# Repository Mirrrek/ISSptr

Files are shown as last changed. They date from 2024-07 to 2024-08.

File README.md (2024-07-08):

# ISSptr

A lil thing that points towards the ISS.

## Required hardware

- [The PCB](https://github.com/Mirrrek/ISSptr/tree/main/schematic), obviously, including:
  - [ESP32-WROOM-32-N4](https://jlcpcb.com/partdetail/EspressifSystems-ESP32_WROOM_32N4/C82899) Microcontroller
  - [QMC5883L](https://jlcpcb.com/partdetail/Qst-QMC5883L/C976032) Magnetometer
  - [ULN2003AD](https://jlcpcb.com/partdetail/TexasInstruments-ULN2003AD/C908113) Transistor Array
  - [AMS1117-3.3](https://jlcpcb.com/partdetail/Advanced_MonolithicSystems-AMS1117_33/C6186) Voltage Regulator
  - [BC817](https://jlcpcb.com/partdetail/Shikues-BC817/C475629) NPN Transistors
  - [TYPE-C-31-M-12](https://jlcpcb.com/partdetail/Korean_HropartsElec-TYPE_C_31_M12/C165948) USB-C Connector
  - [B5B-XH-A(LF)(SN)](https://jlcpcb.com/partdetail/Jst-B5B_XH_A_LF_SN/C157991) Connector
  - Some 0603 resistors and capacitors
- A servo motor (e.g. _SG90_)
- An unipolar stepper motor (e.g. _28BYJ-48_)
- 6-Channel slip ring

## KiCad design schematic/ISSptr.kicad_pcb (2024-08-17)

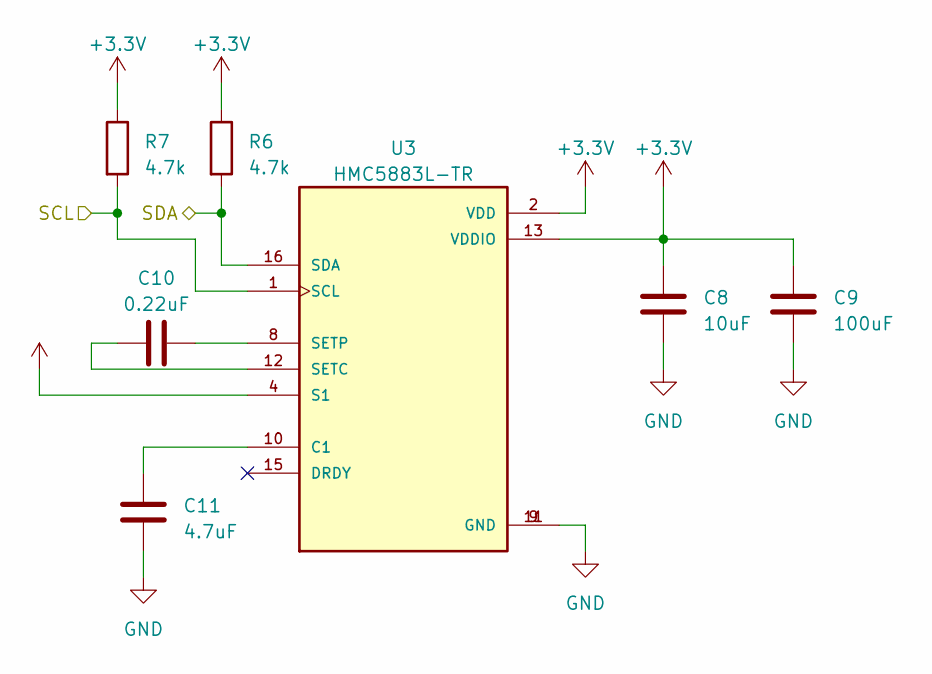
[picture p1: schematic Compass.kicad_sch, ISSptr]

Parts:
C8: 10uF; C_0603_1608Metric; LCSC C19702
C9: 100uF; C_0603_1608Metric; LCSC C730416
C10: 0.22uF; C_0603_1608Metric; LCSC C472764
C11: 4.7uF; C_0603_1608Metric; LCSC C307469
R6, R7: 4.7k; R_0603_1608Metric; LCSC C23162
U3: HMC5883L-TR; XDCR_HMC5883L-TR; PARTREV E; LCSC C976032

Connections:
+3.3V: C8.1, C9.1, R6.1, R7.1, U3.2 (VDD), U3.4 (S1), U3.13 (VDDIO); also elsewhere on the board
/Compass/SCL: R7.2, U3.1 (SCL); also elsewhere on the board
/Compass/SDA: R6.2, U3.16 (SDA); also elsewhere on the board
GND: C8.2, C9.2, C11.1, U3.9 (GND), U3.11 (GND); also elsewhere on the board
unnamed: C11.2, U3.10 (C1)
unnamed: C10.1, U3.12 (SETC)
unnamed: C10.2, U3.8 (SETP)

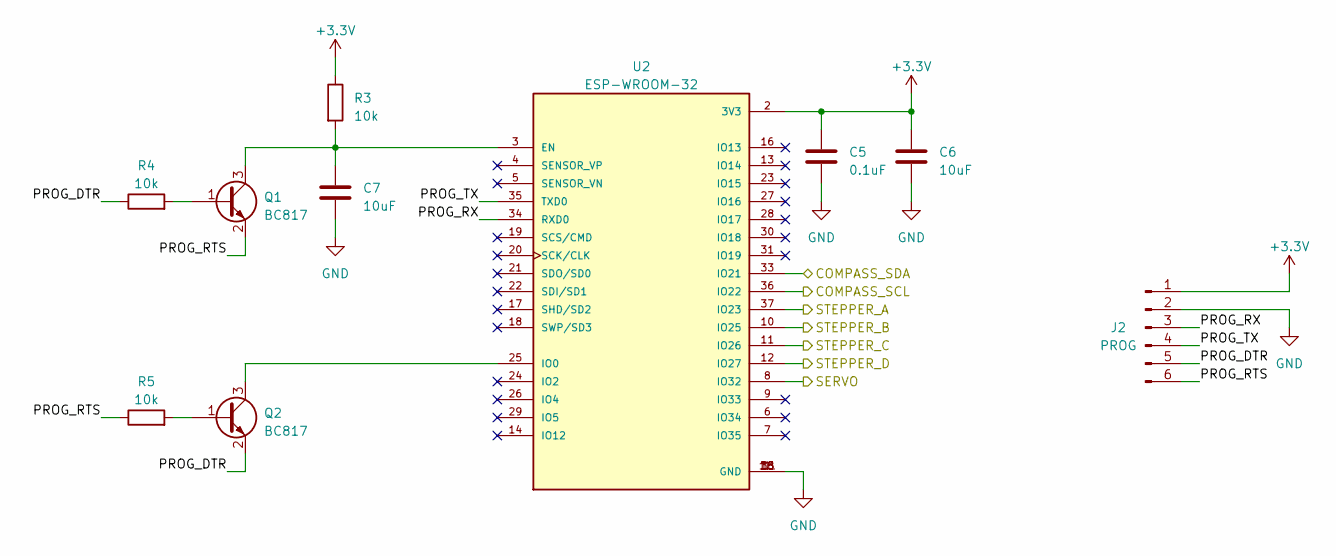
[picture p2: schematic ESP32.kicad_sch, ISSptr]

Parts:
C5: 0.1uF; C_0603_1608Metric; LCSC C1591
C6, C7: 10uF; C_0603_1608Metric; LCSC C19702
J2: PROG; PinHeader_1x06_P2.54mm_Vertical
Q1, Q2: BC817; SOT-23; LCSC C475629
R3, R4, R5: 10k; R_0603_1608Metric; LCSC C25804
U2: ESP-WROOM-32; MODULE_ESP-WROOM-32; LCSC C82899

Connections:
+3.3V: C5.1, C6.1, J2.1, R3.1, U2.2 (3V3); also elsewhere on the board
/Compass/SCL: U2.36 (IO22); also elsewhere on the board
/Compass/SDA: U2.33 (IO21); also elsewhere on the board
/ESP32/PROG_DTR: J2.5, Q2.2 (E), R4.1
/ESP32/PROG_RTS: J2.6, Q1.2 (E), R5.1
/ESP32/PROG_RX: J2.3, U2.34 (RXD0)
/ESP32/PROG_TX: J2.4, U2.35 (TXD0)
/ESP32/SERVO: U2.8 (IO32); also elsewhere on the board
/ESP32/STEPPER_A: U2.37 (IO23); also elsewhere on the board
/ESP32/STEPPER_B: U2.10 (IO25); also elsewhere on the board
/ESP32/STEPPER_C: U2.11 (IO26); also elsewhere on the board
/ESP32/STEPPER_D: U2.12 (IO27); also elsewhere on the board
GND: C5.2, C6.2, C7.2, J2.2, U2.1 (GND), U2.1.1 (GND), U2.15 (GND), U2.38 (GND); also elsewhere on the board
unnamed: Q1.1 (B), R4.2
unnamed: C7.1, Q1.3 (C), R3.2, U2.3 (EN)
unnamed: Q2.1 (B), R5.2
unnamed: Q2.3 (C), U2.25 (IO0)

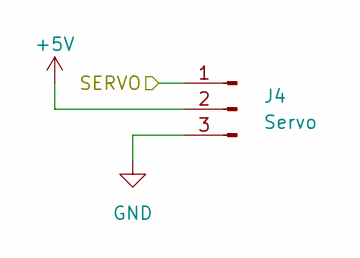
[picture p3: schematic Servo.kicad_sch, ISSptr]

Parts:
J4: Servo; PinHeader_1x03_P2.54mm_Horizontal

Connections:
+5V: J4.2; also elsewhere on the board
/ESP32/SERVO: J4.1; also elsewhere on the board
GND: J4.3; also elsewhere on the board

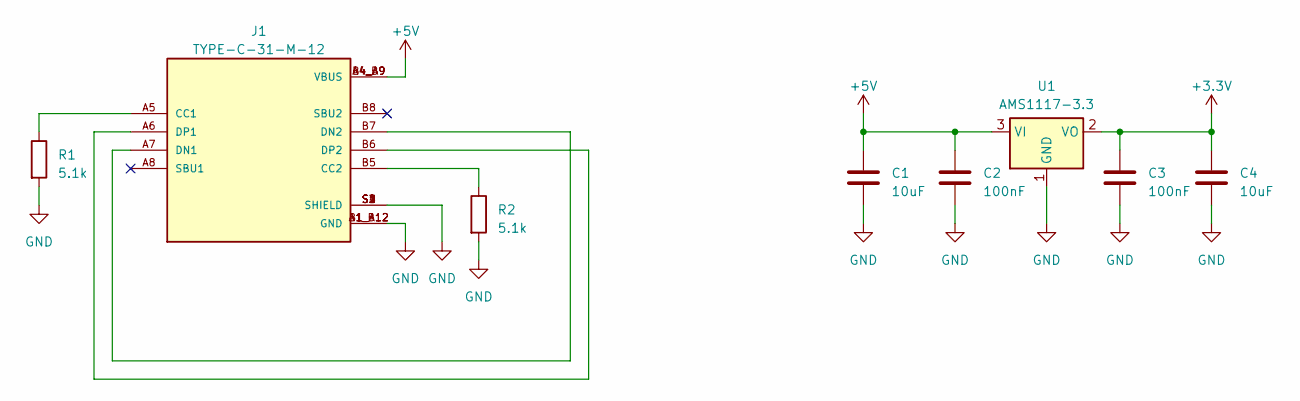
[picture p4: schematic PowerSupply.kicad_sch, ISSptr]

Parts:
C1, C4: 10uF; C_0603_1608Metric; LCSC C19702
C2, C3: 100nF; C_0603_1608Metric; LCSC C1591
J1: TYPE-C-31-M-12; HRO_TYPE-C-31-M-12; PARTREV 2020.12.08; LCSC C165948
R1, R2: 5.1k; R_0603_1608Metric; LCSC C23186
U1: AMS1117-3.3; SOT-223-3_TabPin2; LCSC C6186

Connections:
+3.3V: C3.1, C4.1, U1.2 (VO); also elsewhere on the board
+5V: C1.1, C2.1, J1.A4_B9 (VBUS), J1.B4_A9 (VBUS), U1.3 (VI); also elsewhere on the board
GND: C1.2, C2.2, C3.2, C4.2, J1.A1_B12 (GND), J1.B1_A12 (GND), J1.S1 (SHIELD), J1.S2 (SHIELD), J1.S3 (SHIELD), J1.S4 (SHIELD), R1.2, R2.2, U1.1 (GND); also elsewhere on the board
unnamed: J1.A5 (CC1), R1.1
unnamed: J1.B5 (CC2), R2.1
unnamed: J1.A7 (DN1), J1.B7 (DN2)
unnamed: J1.A6 (DP1), J1.B6 (DP2)

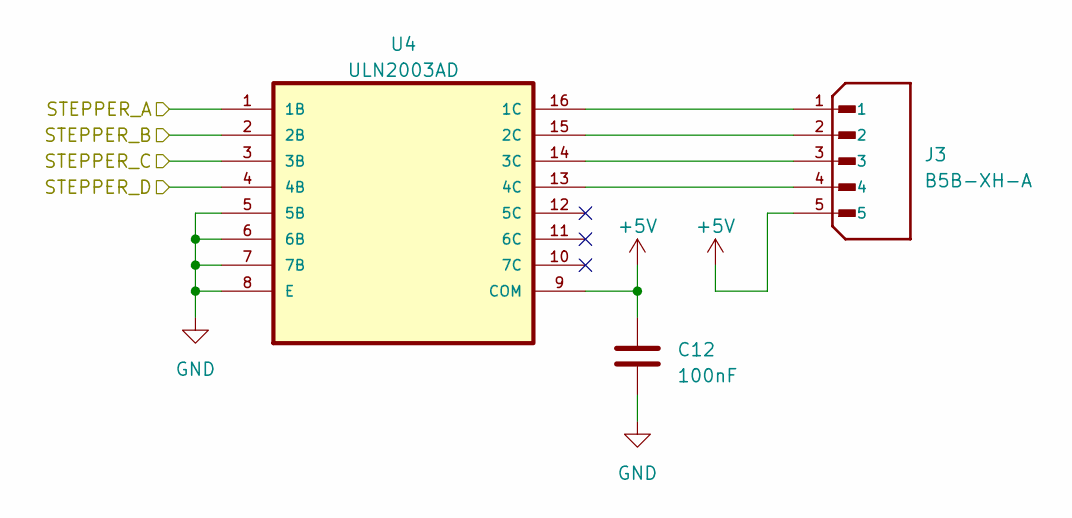
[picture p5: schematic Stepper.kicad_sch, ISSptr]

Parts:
C12: 100nF; C_0603_1608Metric; LCSC C1591
J3: B5B-XH-A; JST_B5B-XH-A_LF__SN_; PARTREV 7/4/21; LCSC C157991
U4: ULN2003AD; SOIC127P600X175-16N; LCSC C908113

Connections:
+5V: C12.1, J3.5, U4.9 (COM); also elsewhere on the board
/ESP32/STEPPER_A: U4.1 (1B); also elsewhere on the board
/ESP32/STEPPER_B: U4.2 (2B); also elsewhere on the board
/ESP32/STEPPER_C: U4.3 (3B); also elsewhere on the board
/ESP32/STEPPER_D: U4.4 (4B); also elsewhere on the board
GND: C12.2, U4.5 (5B), U4.6 (6B), U4.7 (7B), U4.8 (E); also elsewhere on the board
unnamed: J3.1, U4.16 (1C)
unnamed: J3.2, U4.15 (2C)
unnamed: J3.3, U4.14 (3C)
unnamed: J3.4, U4.13 (4C)

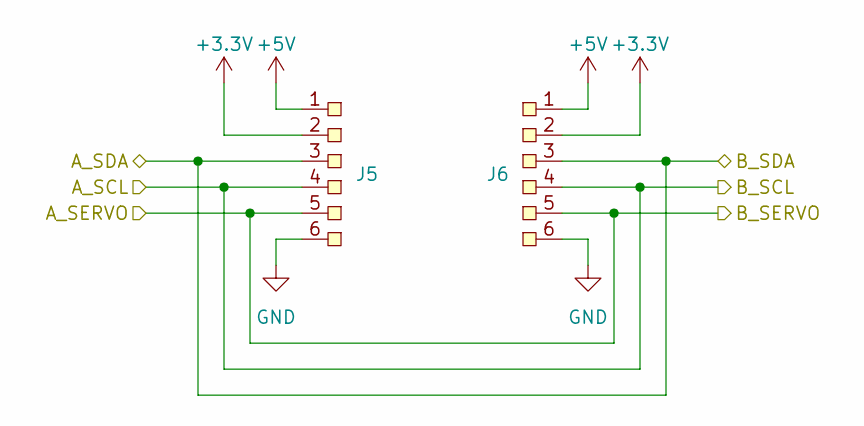
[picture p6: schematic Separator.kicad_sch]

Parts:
J5, J6: SolderPad-6pin

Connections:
+3.3V: J5.2, J6.2; also elsewhere on the board
+5V: J5.1, J6.1; also elsewhere on the board
/Compass/SCL: J5.4, J6.4; also elsewhere on the board
/Compass/SDA: J5.3, J6.3; also elsewhere on the board
/ESP32/SERVO: J5.5, J6.5; also elsewhere on the board
GND: J5.6, J6.6; also elsewhere on the board

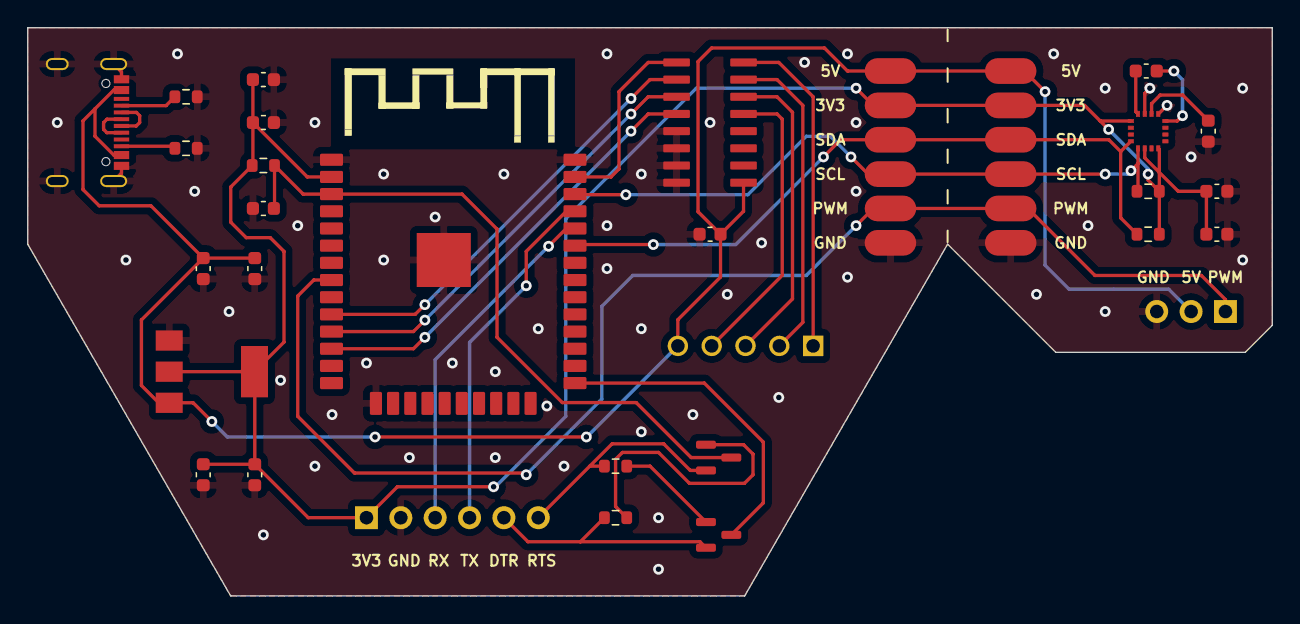
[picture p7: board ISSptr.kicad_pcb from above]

Board: 2 copper layers, 92.0 x 42.0 mm, 31 parts (0 on the bottom side), 29 nets.

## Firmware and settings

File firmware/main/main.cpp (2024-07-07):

#include "compass.hpp"
#include "stepper.hpp"
#include "servo.hpp"
#include "vector.hpp"
#include <freertos/FreeRTOS.h>
#include <freertos/task.h>
#include <esp_log.h>
#include <cmath>
#include <ctime>

#define PIN_COMPASS_SDA GPIO_NUM_21                 /* Compass SDA Pin */
#define PIN_COMPASS_SCL GPIO_NUM_22                 /* Compass SCL Pin */

#define PIN_STEPPER_A GPIO_NUM_16                   /* Stepper Coil 1 Terminal 1 Signal Pin */
#define PIN_STEPPER_B GPIO_NUM_17                   /* Stepper Coil 1 Terminal 2 Signal Pin */
#define PIN_STEPPER_C GPIO_NUM_18                   /* Stepper Coil 2 Terminal 1 Signal Pin */
#define PIN_STEPPER_D GPIO_NUM_19                   /* Stepper Coil 2 Terminal 2 Signal Pin */

#define PIN_SERVO GPIO_NUM_23                       /* Servo Signal Pin */

#define STEPPER_STEPS_PER_REVOLUTION 2048           /* Number of steps per full revolution of stepper */

#define COMPASS_MAX_FIELD_STRENGTH 0.5f             /* Maximum magnetic field strength considered natural (no interference) */
#define COMPASS_MAX_Z 0.25f                         /* Maximum z component of compass vector considered flat */

#define ISS_POSITION_FETCH_INTERVAL 24 * 60 * 60    /* Interval (s) of ISS position re-fetch from API */

#define COORDINATES_LAT 0.0f                        /* Latitude of user */
#define COORDINATES_LON 0.0f                        /* Longitude of user */

static const char* TAG = "main";

Vector3 latLongToVector3(float lat, float lon);
Vector3 project(Vector3 vector, Vector3 normal);
float angle(Vector3 a, Vector3 b);

extern "C" void app_main() {
    ESP_LOGI(TAG, "Initializing...");

    Compass compass(PIN_COMPASS_SDA, PIN_COMPASS_SCL);
    Stepper stepper(PIN_STEPPER_A, PIN_STEPPER_B, PIN_STEPPER_C, PIN_STEPPER_D);
    Servo servo(PIN_SERVO, true);

    Vector3 userPosition = latLongToVector3(COORDINATES_LAT, COORDINATES_LON);
    Vector3 northPoleProjected = project(Vector3(0.0f, 0.0f, 1.0f), userPosition);

    time_t lastIssPositionFetch = 0;

    ESP_LOGI(TAG, "Starting...");

    while (true) {
        ESP_LOGD(TAG, "Updating...");

        time_t currentTime = time(nullptr);
        if (currentTime - lastIssPositionFetch > ISS_POSITION_FETCH_INTERVAL) {
            ESP_LOGI(TAG, "Fetching ISS position...");

            // TODO: Fetch ISS position from API

            lastIssPositionFetch = currentTime;
        }

        Vector3 issPosition = latLongToVector3(0.0f /* TODO: Set ISS latitude */, 0.0f /* TODO: Set ISS longitude */);
        Vector3 issDirectionProjected = project(issPosition - userPosition, userPosition);

        Vector3 compassVector = compass.read();

        if (compassVector.length() > COMPASS_MAX_FIELD_STRENGTH) {
            ESP_LOGW(TAG, "Magnetic field strength too high");
            vTaskDelay(pdMS_TO_TICKS(1000));
            continue;
        }

        if (abs(compassVector.z) > COMPASS_MAX_Z) {
            ESP_LOGW(TAG, "Compass not flat");
            vTaskDelay(pdMS_TO_TICKS(1000));
            continue;
        }

        float compassAngle = angle(Vector3(compassVector.x, compassVector.y, 0.0f), Vector3(1.0f, 0.0f, 0.0f));

        float issAngle = angle(userPosition, issPosition);
        servo.set(issAngle);

        float northPoleToIssAngle = angle(northPoleProjected, issDirectionProjected);
        stepper.move((compassAngle + northPoleToIssAngle) / 360.0f * STEPPER_STEPS_PER_REVOLUTION);
    }
}

Vector3 latLongToVector3(float lat, float lon) {
    float latRad = lat / 180.0f * M_PI;
    float lonRad = lon / 180.0f * M_PI;

    return Vector3(cos(latRad) * cos(lonRad), cos(latRad) * sin(lonRad), sin(latRad));
}

Vector3 project(Vector3 vector, Vector3 normal) {
    return vector - normal * vector.dot(normal);
}

float angle(Vector3 a, Vector3 b) {
    return acos(a.dot(b) / (a.length() * b.length())) / M_PI * 180.0f;
}

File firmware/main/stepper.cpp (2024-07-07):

#include "stepper.hpp"
#include <freertos/FreeRTOS.h>
#include <freertos/task.h>
#include <rom/ets_sys.h>
#include <esp_log.h>

#define STEP_DELAY_US 3500

static const char* TAG = "stepper";

Stepper::Stepper(gpio_num_t a, gpio_num_t b, gpio_num_t c, gpio_num_t d) {
    _a = a;
    _b = b;
    _c = c;
    _d = d;
    _state = A;

    ESP_LOGI(TAG, "Initializing stepper on pins %d, %d, %d, %d", _a, _b, _c, _d);

    gpio_config_t config = {
        .pin_bit_mask = (1ULL << _a) | (1ULL << _b) | (1ULL << _c) | (1ULL << _d),
        .mode = GPIO_MODE_OUTPUT,
        .pull_up_en = GPIO_PULLUP_DISABLE,
        .pull_down_en = GPIO_PULLDOWN_DISABLE,
        .intr_type = GPIO_INTR_DISABLE
    };

    gpio_config(&config);

    _clear();
}

void Stepper::move(int16_t steps) {
    ESP_LOGD(TAG, "Moving stepper on pins %d, %d, %d, %d by %d steps", _a, _b, _c, _d, steps);

    bool direction = steps > 0;

    for (int16_t i = 0; i < (direction ? steps : -steps); i++) {
        if (i % 1024 == 1023) {
            vTaskDelay(pdMS_TO_TICKS(50));
        }

        _step(direction);
    }

    _clear();
}

void Stepper::_step(bool direction) {
    _state = (State)((direction ? _state + 1 : _state + 7) % 4);

    switch (_state) {
    case A:
        gpio_set_level(_a, 1);
        gpio_set_level(_b, 0);
        gpio_set_level(_c, 0);
        gpio_set_level(_d, 0);
        break;
    case B:
        gpio_set_level(_a, 0);
        gpio_set_level(_b, 1);
        gpio_set_level(_c, 0);
        gpio_set_level(_d, 0);
        break;
    case C:
        gpio_set_level(_a, 0);
        gpio_set_level(_b, 0);
        gpio_set_level(_c, 1);
        gpio_set_level(_d, 0);
        break;
    case D:
        gpio_set_level(_a, 0);
        gpio_set_level(_b, 0);
        gpio_set_level(_c, 0);
        gpio_set_level(_d, 1);
        break;
    }

    ets_delay_us(STEP_DELAY_US);
}

void Stepper::_clear() {
    gpio_set_level(_a, 0);
    gpio_set_level(_b, 0);
    gpio_set_level(_c, 0);
    gpio_set_level(_d, 0);
}

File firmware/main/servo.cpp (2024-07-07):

#include "servo.hpp"
#include <esp_log.h>

#define NORMAL_RANGE_OFFSET 0.05f
#define REGULAR_RANGE_COEFFICIENT 0.0002777777777f
#define WIDE_RANGE_OFFSET 0.025f
#define WIDE_RANGE_COEFFICIENT 0.0005555555555f

#define DUTY_RESOLUTION LEDC_TIMER_10_BIT

static const char* TAG = "servo";

bool Servo::_timerInitialized = false;
uint8_t Servo::_instanceCount = 0;

Servo::Servo(gpio_num_t pin, bool wideRange) {
    _pin = pin;
    _wideRange = wideRange;

    if (!_timerInitialized) {
        ESP_LOGI(TAG, "Initializing LEDC timer");

        ledc_timer_config_t config = {
            .speed_mode = LEDC_HIGH_SPEED_MODE,
            .duty_resolution = DUTY_RESOLUTION,
            .timer_num = LEDC_TIMER_0,
            .freq_hz = 50,
            .clk_cfg = LEDC_AUTO_CLK,
            .deconfigure = false
        };

        ledc_timer_config(&config);

        ledc_fade_func_install(0);

        _timerInitialized = true;
    }

    this->_channel = (ledc_channel_t)(LEDC_CHANNEL_0 + _instanceCount++);

    ESP_LOGI(TAG, "Configuring pin %d (channel %d)", _pin, _channel);

    ledc_channel_config_t config = {
        .gpio_num = _pin,
        .speed_mode = LEDC_HIGH_SPEED_MODE,
        .channel = _channel,
        .intr_type = LEDC_INTR_DISABLE,
        .timer_sel = LEDC_TIMER_0,
        .duty = 0,
        .hpoint = 0,
        .flags = 0
    };

    ledc_channel_config(&config);
}

void Servo::set(float angle) {
    if (angle < 0.0f) {
        ESP_LOGW(TAG, "Invalid angle: %f, clamping to 0", angle);
        angle = 0.0f;
    }

    if (angle > 180.0f) {
        ESP_LOGW(TAG, "Invalid angle: %f, clamping to 180", angle);
        angle = 180.0f;
    }

    ESP_LOGD(TAG, "Setting angle on pin %d to %f", _pin, angle);

    float offset = _wideRange ? WIDE_RANGE_OFFSET : NORMAL_RANGE_OFFSET;
    float coefficient = _wideRange ? WIDE_RANGE_COEFFICIENT : REGULAR_RANGE_COEFFICIENT;

    float duty = offset + angle * coefficient;

    ledc_set_duty_and_update(LEDC_HIGH_SPEED_MODE, _channel, (uint32_t)(duty * (1 << DUTY_RESOLUTION)), 0);
}

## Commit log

2024-07-07 Initialize development environment
    [ISSptr.kicad_pcb, ISSptr.kicad_sch]
2024-07-07 Add servo library
2024-07-07 Add stepper library
2024-07-07 Fix compass library code
    [compass.cpp]
2024-07-07 Create schematic layout
    [Compass.kicad_sch, ESP32.kicad_sch, ISSptr.kicad_sch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]
2024-07-08 Create power supply schematic
    [PowerSupply.kicad_sch]
2024-07-08 Create ESP32 schematic
    [ESP32.kicad_sch, ISSptr.kicad_sch]
2024-07-08 Create separator schematic
    [ISSptr.kicad_sch, Separator.kicad_sch]
2024-07-08 Create compass schematic
    [Compass.kicad_sch, ISSptr.kicad_sch, Separator.kicad_sch]
2024-07-08 Create servo header schematic
    [ISSptr.kicad_sch, Servo.kicad_sch]
2024-07-08 Create stepper driver schematic
    [ISSptr.kicad_sch, Stepper.kicad_sch]
2024-07-08 Assign footprints
    [Compass.kicad_sch, ESP32.kicad_sch, PowerSupply.kicad_sch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]
2024-07-08 Lay out PCB
    [ISSptr.kicad_pcb]
2024-07-08 Remove component outlines on silkscreen
    [ISSptr.kicad_pcb]
2024-07-08 Trace PCB
    [ISSptr.kicad_pcb]
2024-07-08 Setup PCB for production
    [Compass.kicad_sch, ESP32.kicad_sch, ISSptr.kicad_pcb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]
2024-08-17 Reduce PCB footprint
    [ISSptr.kicad_pcb]
2024-08-17 Route PCB
    [ISSptr.kicad_pcb]
